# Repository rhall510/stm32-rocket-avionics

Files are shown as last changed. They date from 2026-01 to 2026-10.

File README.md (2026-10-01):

# STM32-based rocket avionics unit and active tracking ground station

 

> **⚠️ NOTE: This project is currently in active development.**
> See the [project plan](docs/PROJECT_PLAN.md) for a detailed roadmap and the [development log](docs/DEVELOPMENT_LOG.md) for regular progress updates.

---

## Overview
This project aims to build a robust avionics unit for high power model rocketry. This system will also include a ground station that mechanically rotates a high gain antenna to actively track the rocket in real time during flight and receive critical telemetry data.

The system relies on sensor fusion for onboard state estimation and uses a hybrid RF tracking method combining position/movement telemetry received from the rocket and ranging with several ground nodes to accurately place the rocket.

## Key features
* **Dual-band telemetry:**
    * **2.4GHz (SX1280):** High bandwidth telemetry and ranging.
    * **868MHz (SX1262):** Command link.
* **Active ground tracking:** Motorized base with PID control tracks the rocket's position automatically using two independent data sources (on board avionics and ground ranging).
* **Live updating GUI:** See all relevant statistics and flight path updates in real time.
* **Advanced firmware:** Built on STM32 using FreeRTOS for concurrent sensor data acquisition, data logging, RF transmission, and parachute deployment.
* **Safety first:** Robust pre-flight check routine, redundant parachute deployment logic, and failsafe state management.

## System architecture
The project is divided into three main subsystems:

1.  **Avionics (Rocket):** Onboard PCB with flight sensors, NOR flash logging, and RF transceivers controlled by a STM32G474 microcontroller.
2.  **Ground station:** Network consisting of ranging nodes and a central controlling node with a motorised tracking base utilizing position telemetry to maintain a high gain link with the rocket.
3.  **Control center:** PC based GUI for live data visualization and controlling the ground station and avionics unit.

```mermaid
---
config:
  theme: neo-dark
  layout: dagre
---
flowchart TB
 subgraph Rocket["Avionics Unit"]
        MCU_R["MCU<br>STM32G474"]
        Sensors["Sensors<br>IMU, GPS, Baro"]
        NOR["NOR flash"]
        RKT_24["SX1280 2.4GHz"]
        RKT_868["SX1262 868MHz"]
        Parachute["Parachute<br>deployment"]
  end
 subgraph Air["Ground station (controller)"]
        GS_24["SX1280 2.4GHz"]
        GS_PDOA@{ label: "<span style=\"padding-left:\">SX1262 868MHz</span>" }
        MCU_G@{ label: "MCU<span style=\"padding-left:\"><br>STM32G474</span>" }
        Motors["Stepper/Servo<br>tracker base"]
        GUI["Qt GUI<br>Data display and<br> mission control"]
  end
 subgraph s1["Ground station (ranging nodes x2)"]
        n1["SX1280 2.4GHz<br>Ranging"]
        n2@{ label: "<span style=\"padding-left:\">SX1262 868MHz</span>" }
        n3@{ label: "MCU<span style=\"padding-left:\"><br>STM32G474</span>" }
  end
    Sensors -- SPI/I2C --> MCU_R
    MCU_R -- SPI --> RKT_868 & NOR
    MCU_R <-- SPI --> RKT_24
    MCU_R -- GPIO --> Parachute
    RKT_24 -. Telemetry .-> GS_24
    RKT_868 <-. Cmd .-> GS_PDOA
    GS_24 <-- SPI --> MCU_G
    GS_PDOA <-- SPI --> MCU_G
    MCU_G -- GPIO/PWM --> Motors
    MCU_G <-. USB .-> GUI
    GS_24 <-. Ranging .-> RKT_24
    n1 <-- SPI --> n3
    n2 <-- SPI --> n3
    n2 <-. Cmd .-> GS_PDOA

    GS_PDOA@{ shape: rect}
    MCU_G@{ shape: rect}
    n1@{ shape: rect}
    n2@{ shape: rect}
    n3@{ shape: rect}
```

## Repository structure
* `docs/`: Progress logs, planning documents, and testing data.
* `firmware/`: Source code for the avionics and ground station MCUs as well as other prototyping code.
* `hardware/`: KiCad schematics and PCB layouts.
* `mechanical/`: Model files for making various non-electrical parts of the project.
* `software/`: Source code for the control center GUI application.

## Current status
Goals from the [project plan](docs/PROJECT_PLAN.md) that are currently being worked on:

##### 2\. Avionics unit
* [ ] Implement and test parachute deployment logic.
* [ ] Final field tests of full avionics unit.

*For an up to date breakdown of progress, check the [development log](docs/DEVELOPMENT_LOG.md).*

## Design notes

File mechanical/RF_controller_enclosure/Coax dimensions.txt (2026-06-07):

2.4GHz = 55mm coax length (start at 75mm - 10mm for connectors each end)
868MHz = 195mm coax length (start at 215mm - 10mm for connectors each end)

SMA connector assembly:
- Cut outer jacket 10mm from end
- Expose inner conductor 3mm
- Solder inner pin
- Add outer part and crimp on ferrule 
- Heat shrink

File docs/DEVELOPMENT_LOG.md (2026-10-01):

# **Progress log**

Regular detailed progress logs will be written here. Most recent at the top.

---
### October 1st 2026

The avionics part of the project is essentially complete (except for one remaining bug which I'm working to fix currently)! Here is a breakdown of the progress made since the last update:

#### Data integration algorithm

I started by prototyping the data integration algorithms needed to transform the raw data from sensors into a live position estimate in python. I decided to go with a 3 Kalman filter approach which each handle different parts of the tracking. These are:
- A Multiplicative Extended Kalman Filter (MEKF) for integrating gyroscope, accelerometer, and magnetometer data into an orientation estimate.
- A 2D standard Kalman filter for integrating accelerometer and GPS data into a horizontal position and velocity estimate.
- A 1D standard Kalman filter for integrating accelerometer, barometer, and GPS data into a vertical position and velocity estimate.

I used raw data recorded in multiple test runs of moving the avionics unit around in different ways to test the accuracy of these filters and tune parameters to get the best results. In the end I managed to get a fairly accurate result for the total position and orientation estimate which, while not perfect, did track my movements in the tests quite well.

#### Data integration results from a walk test

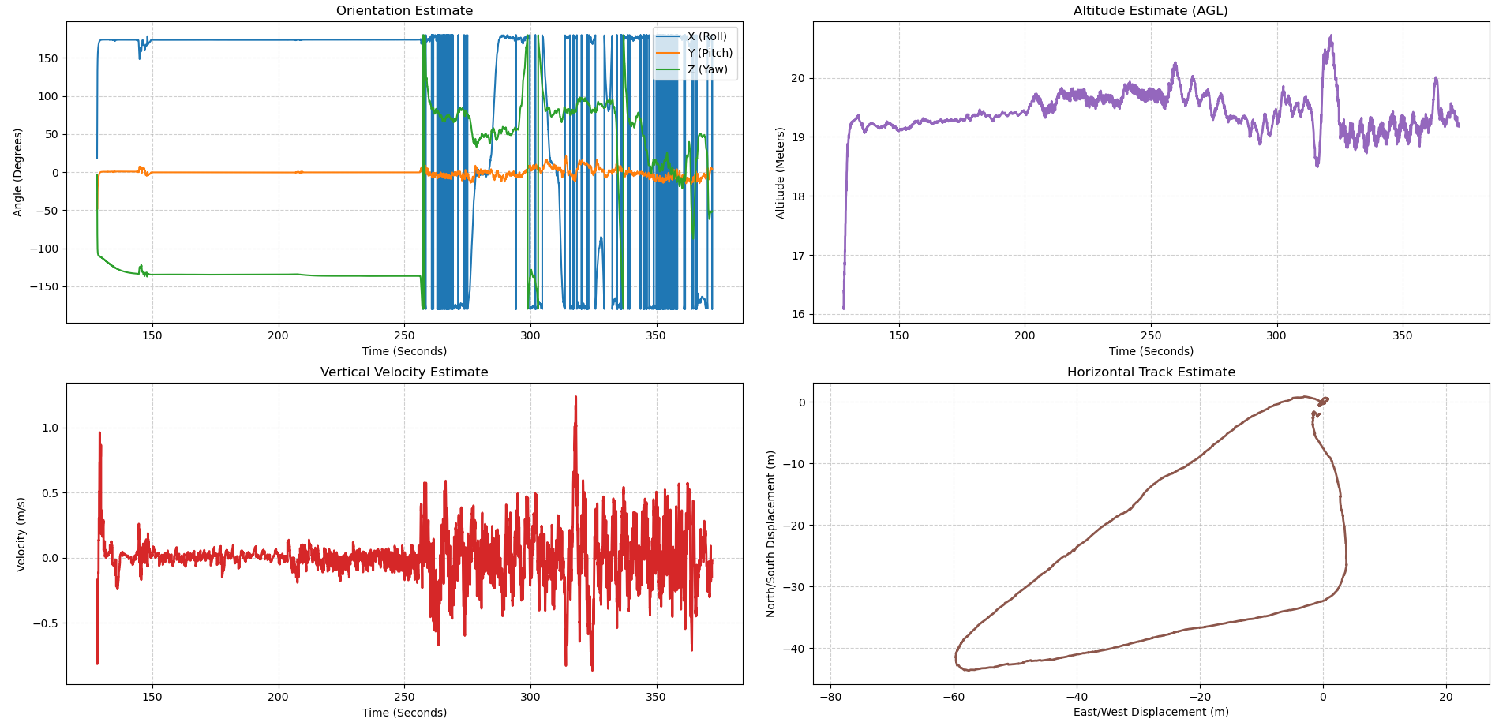
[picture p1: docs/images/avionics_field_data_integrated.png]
Data integration plots


The plots above show the results of applying these filters to the raw data aquired from a test where I walked around a track approximately 200m in length holding the avionics unit and occasionally performing other movements like rotating the unit or moving it up and down rapidly.

The vertical filter is the most accurate as the frequent low noise pressure readings can easily keep the position estimate in check to prevent accelerometer drift while the GPS prevents long term drift as ambient pressure changes slowly. This tracks the actual altitude very precisely and can capture small movements of less than a meter well.

The orientation filter is also good though it does suffer from some drift over longer periods of constant movement as during these periods the accelerometer cannot be used as a second reference vector to dampen gyroscope drift. Over the timescales expected for a model rocket flight (1-2 mins) this drift will likely not be enough to cause major issues, especially as the rocket is expected to rotate during flight which will help distribute the magnetic vectors drift correction across all axes of rotation.

The horizontal filter is the least accurate part of the system and does pose some potential problems for an actual rocket flight. The main reason for this is due to the unforgiving nature of relying mostly on the accelerometer for dead reckoning between GPS updates. There is rapid accumulation of accelerometer drift due to noise and errors in the orientation estimate leaking acceleration into the hoirizontal axes which causes a spiky looking trajectory on the horizontal plane. The drift gets substantially worse when there is rapid rotation of the avionics unit which is likely due to the fact that the rotation of the unit imparts some centrifugal force on the accelerometers which are not centered. When GPS is active however it is able to contain this drift very well and it is still able to maintain an accurate estimate of horizontal position, with possible drift of a few meters from the actual position. In an actual rocket flight which covers much larger distances than these shorter walk tests errors of this scale will be hardly noticeable.

However, GPS lock is likely to be lost during the boost phase of flight due to the high acceleration which then poses a risk of severe drift between the time GPS lock is lost and regained. Currently I plan to combat this using the network of ranging nodes planned for later in the project. These ranging nodes act as a second measurement of both vertical and horizontal position and therefore can be integrated into the Kalman filters. Ranging position estimates will be more accurate the closer the rocket is to the ground and should still work perfectly during the boost phase. Therefore, I can use the position estimate provided by the ranging nodes to correct position while the rocket is low to the ground and GPS lock is lost, then later in flight when the rocket is higher up and GPS lock is regained it can start using GPS again. In this way the two measurements cover each others weaknesses and allows a position measurement to be obtained throughout the flight to prevent drift.

#### Live telemetry on the avionics unit

So with the data integration algorithm fully prototyped I then translated it over to the avionics unit so it could run in real time. I used the CMSIS-DSP library to handle most of the matrix operations for it's high efficiency and manually coded helper functions for quaternion operations as in the prototype. I then expanded the network functions to add commands that control the telemetry output of the avionics unit via the controller node. First the home position command must be sent which instructs the avionics unit to collect samples from the barometer and GPS to set the position it is at currently as the reference position to measure displacement from. This must be done first and the unit will refuse to start telemetry without first setting the home position as a safety check. Once this is done another command can be sent to start telemetry collection which will instruct the avionics unit to wipe previously stored flight data and start up all sensors. It will then integrate all received data and periodically send back it's current estimate of position, velocity, orientation, temperature, and pressure to the controller node. The controller can then relay this data to the host PC which runs a script to display the data live.

#### Live telemetry test showing good tracking interrupted periodically by large erroneous spikes

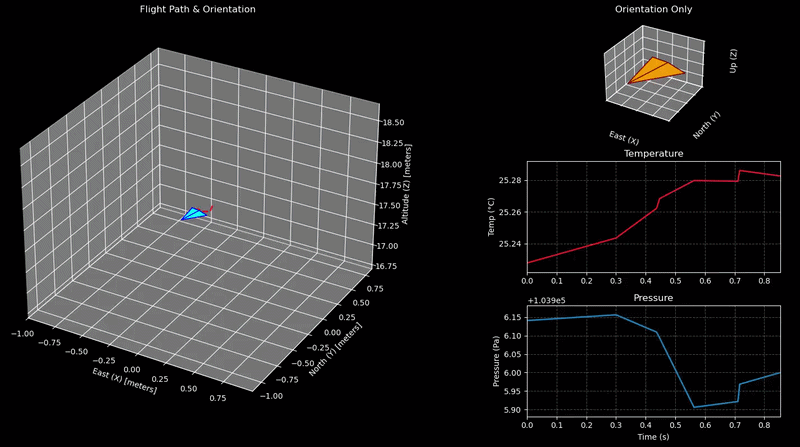
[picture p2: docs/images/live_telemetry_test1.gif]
Live telemetry test


The GIF above shows the actual live data received from the avionics unit during a test where I walked it along the same track as the previous test. The telemetry shows it follows the track very well overall but there are clear spikes in the data which appear to happen at random. Looking at the raw data reveals that these erroneous values appear in all the data types (position, velocity, orientation, temp/press) and they appear more often when the avionics unit was further from the controlling node. In addition, the raw data downloaded from the test does not show these spikes and the estimates for all data cleanly return to the real values immediately after each spike. Therefore, it is very likely these errors are being introduced in the transmission of the data from the avionics unit to the controlling node, rather than an issue with the data or integration algorithm itself. Currently I think this is likely due to the fact that the controlling node relays all packets without checking for CRC errors beforehand. I plan to add this check and run another test to see if this fixes the error ASAP.

Other than that issue however, the live telemetry link works perfectly!

#### Flight state machine

To support the parachute deployment logic a state machine was implemented to track the current stage of flight the eventual model rocket is in. It consists of 5 states with the following transition rules:

- PAD STATE: Transition to boost state when velocity and altitude are above thresholds
- BOOST STATE: Transition to coast state when acceleration (ignoring gravity) drops below threshold
- COAST STATE: Transition to descent state when vertical velocity goes negative
- DESCENT STATE: Transition to landed state when altitude and velocity are below thresholds
- LANDED STATE: No transition

The transition from coast to descent state triggers the parachute deployment logic.

I have not currently tested this state machine but I plan to as soon as possible. I would like to get a drone and attach the avionics unit to it to be able to collect data on larger and faster movements more similar to what might be expected for a model rocket launch.

---
### July 17th 2026

The data calibration stage has been completed successfully! I have written 3 python scripts which take in the raw binary data downloaded from the avionics unit and use it to calibrate the magnetometer, both accelerometers, and the gyroscope.

The gyroscope is the easiest to calibrate. Although scale factor and cross axis alignment issues can exist for gyroscopes, they are generally quite well calibrated from the factory, and it isn't really practical for me to make the precise setup required to calibrate these things without launching an entirely new project. Therefore, I decided to only focus on the other easy thing to calibrate which is the zero-rate offset. For this I recorded some data for around a minute while the unit was sitting perfectly still. The first and last 2 seconds of the data is filtered out to remove spikes caused by the pressing of the start/stop button from affecting the calibration. Then the average value for each axis was simply averaged and negated to get the offset that needs to be added to each reading. Below is the results of calibrating the gyroscope data:

#### Gyroscope calibration

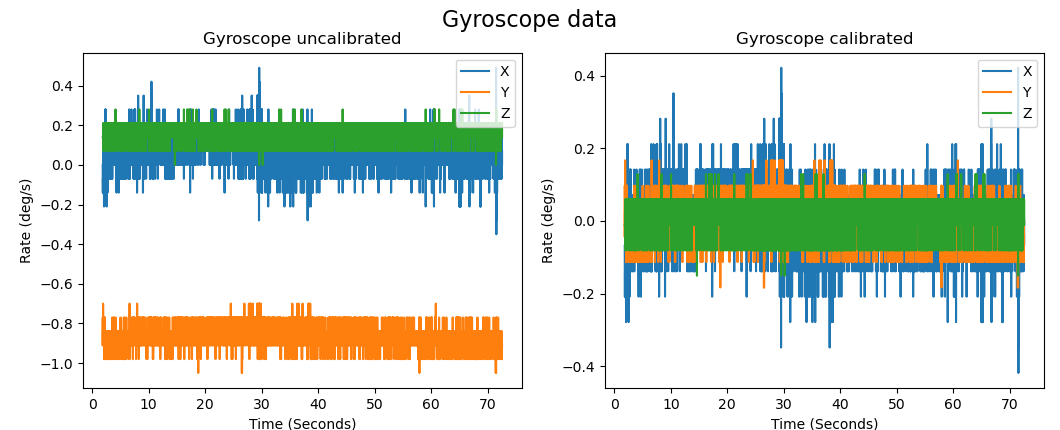
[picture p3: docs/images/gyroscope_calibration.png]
Gyroscope calibration


Next is the magnetometer. For this I used an ellipsoid fitting algorithm to correct both hard and soft iron interference. This algorithm uses least squares to fit an ellipsoid to the uncalibrated data, and then find the transforms needed to turn the ellipsoid back into a unit sphere centered at the origin. Data was collected by taking measurements continuously while I spun the unit around in my hands at all angles. Below is the results of calibrating the magnetometer data:

#### Magnetometer calibration (red wireframe is the ideal unit sphere with a red cross at it's center)

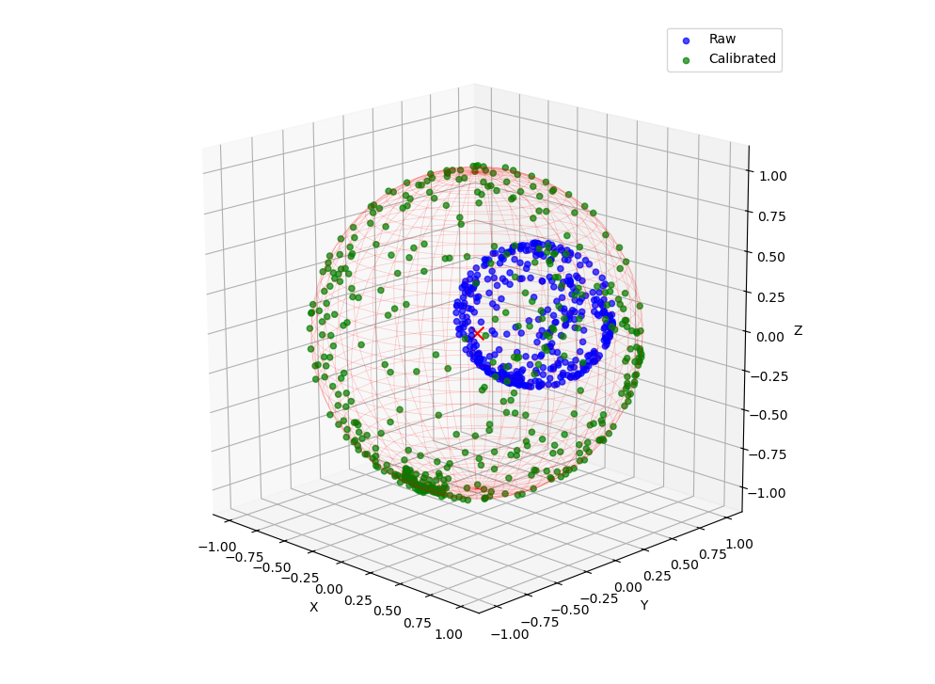
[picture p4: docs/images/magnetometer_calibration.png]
Magnetometer calibration


Finally, the accelerometers. For this I use the same ellipsoid fitting algorithm as used for the magnetometer, but with some differences in data collection and processing before calibration. While the magnetometer measures Earths magnetic field and is not affected by the movement of my hand when rotating it, the accelerometers measure gravity PLUS any additional movement when rotating it around. This will obviously throw off the calibration as it expects the magnitude of the measured force to be exactly 1, so I adapted my strategy to get more stable readings. Instead of rotating the unit in my hands, I 3d printed a roll cage which holds the avionics unit in it's enclosure rigidly in the center. This can then be placed in a bowl and rotated to any angle, and there is enough friction to hold it perfectly still.

#### Accelerometer calibration roll cage in a plastic bowl with the avionics unit held in the center

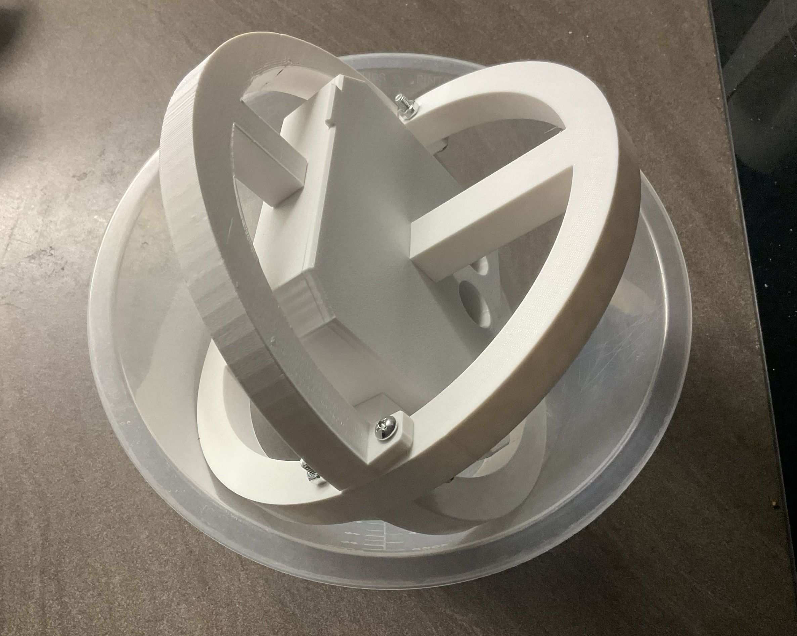
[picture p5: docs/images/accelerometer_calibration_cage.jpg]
Accelerometer calibration roll cage


Data was recorded continuously as I rotated the unit to various angles in the bowl, stopping for a few seconds at each angle to allow all vibrations to settle and get a stable reading. Of course, the raw data now contains both the stable periods and the movement when I'm rotating it in the bowl, so before calibration I added logic to first filter out all the unstable periods. To do this I calculated the variance with a rolling window of 50 measurements (half a second), and selected only data where the variance is below a threshold. I also added an additional filter to remove data recorded within 100ms of the threshold being crossed (either at the beginning or end of a settled period) as an additional buffer against including bad data. This gave nice clean measurements at various angles from only periods where the unit was completely settled.

The high-G accelerometer presented an additional problem because it has a very high baseline of noise in this low acceleration environment, meaning settled periods could not be picked out due to the noise completely swamping out the additional variance caused by movements. Therefore, I utilised the timestamps of the settled periods determined from the low-G data to filter the high-G data to only include measurements done within these same periods. This was not enough however, as the extremely high baseline noise meant an ellipsoid could not be fit well to the data, even after filtering. Therefore, an additional averaging step was introduced. For each settled period, all measurements were averaged to produce a single more stable measurement. This was done for both the high and low G data for consistency. Using this averaging method, I was able to get a good ellipsoid fit from 38 data points (one for each settled orientation) and nicely correct the high-G accelerometer data despite the extreme noise level. Below is the results of calibrating the accelerometer data:

#### Accelerometer calibration (red wireframe is the ideal unit sphere with a red cross at it's center)

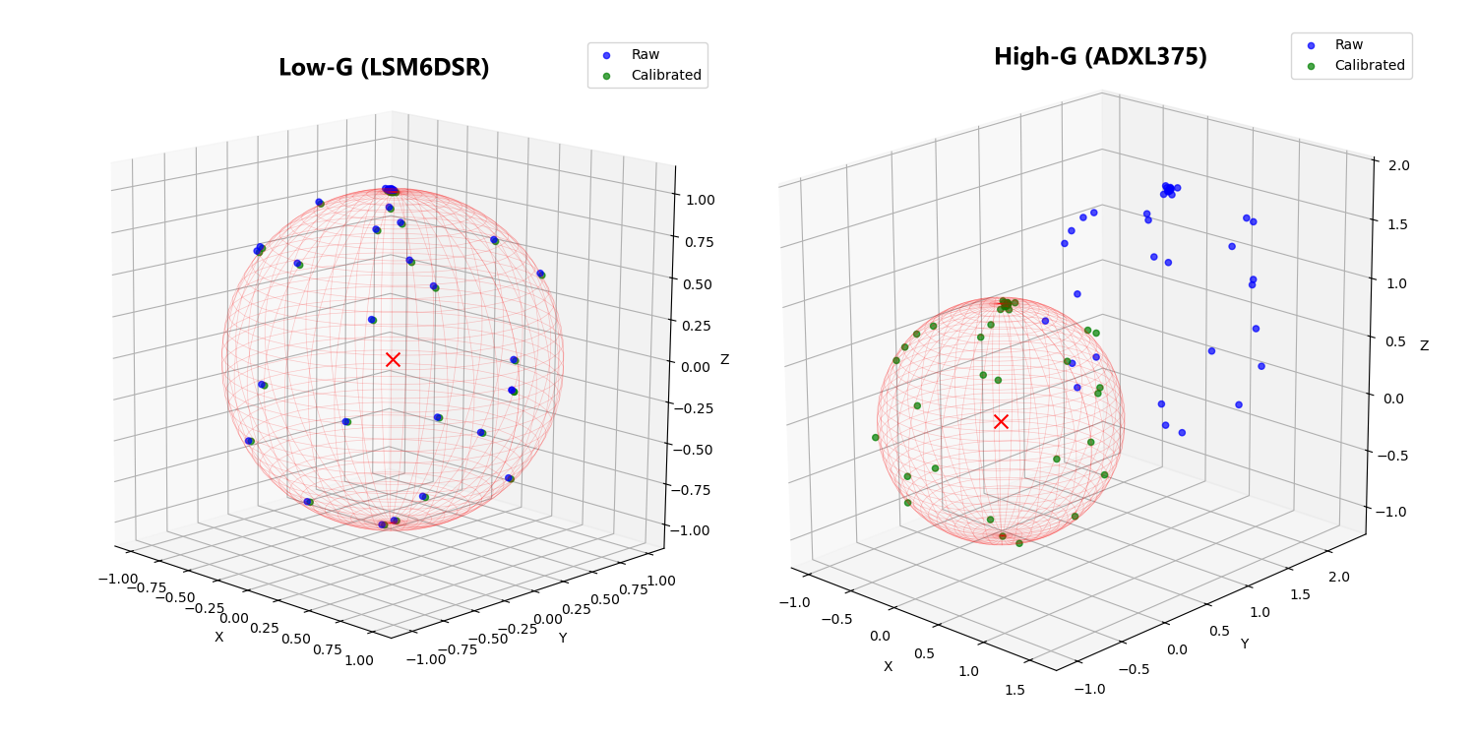
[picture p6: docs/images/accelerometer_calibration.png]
Accelerometer calibration


---
### July 16th 2026

Over the past ~2 weeks I have been working on the goals I set in the last update, and I'm happy to say all of them have now been completed!

#### Improved antenna design

After a few attempts I managed to successfully make and tune a pair of 868MHz sleeve dipole antennas. I made them by stripping a piece of RG316 coax cable to remove all but the inner conductor for around 80mm to make the top half of the dipole. Then I used a piece of 6mm diameter 0.5mm thickness copper tubing cut to around the same length for the second half of the dipole, soldered to the outer braid at the base of the exposed inner conductor portion. To keep the coax centered in the tubing I applied a few layers of heat shrink at 2 points along the length of the coax to be covered by the tubing, ensuring they were as thin as possible to not affect the velocity factor of the gap too much (this was learned the hard way with one failed attempt that used far too much heat shrink!). I also covered the exposed inner conductor in heat shrink for added stability and protection. I left a bit of length under the tubing to clip on a ferrite bead and then soldered an SMA male connector before tuning using a nanoVNA. After tuning, the inner conductor has a final length of 82mm and the tubing has a final length of 73mm.

I then 3d printed some enclosures to protect and stabilise the antennas further. These enclosures do slightly detune the antennas, making their resonant frequency decrease slightly, but the SWR at 868MHz is still <2.0 so I plan to leave them as they are currently until I know the exact final design of their environment so I can perfectly tune them at that point.

#### Sleeve dipole design (top: uncovered, bottom: in enclosure)

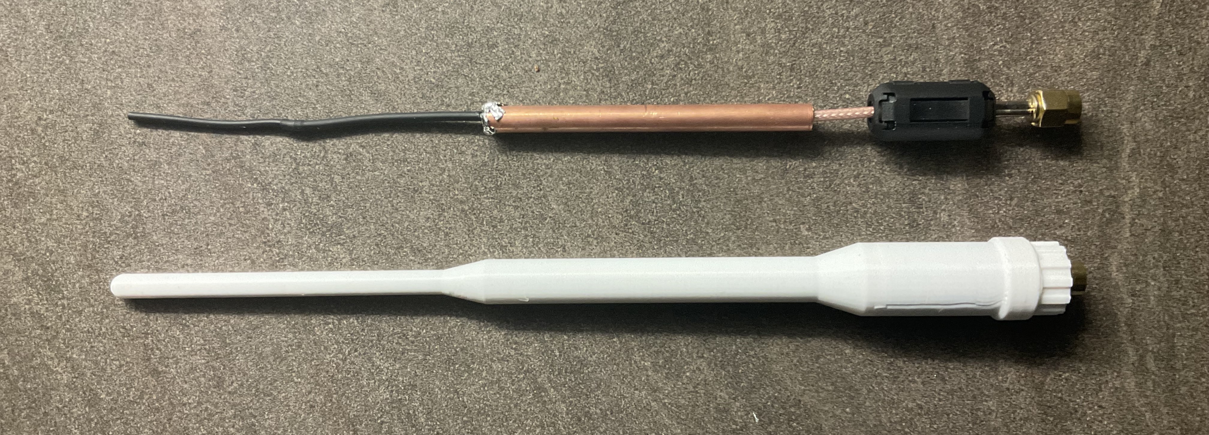
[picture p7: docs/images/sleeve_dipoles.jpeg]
Sleeve dipoles


#### Sleeve dipole final tuned nanoVNA reading (no enclosure)

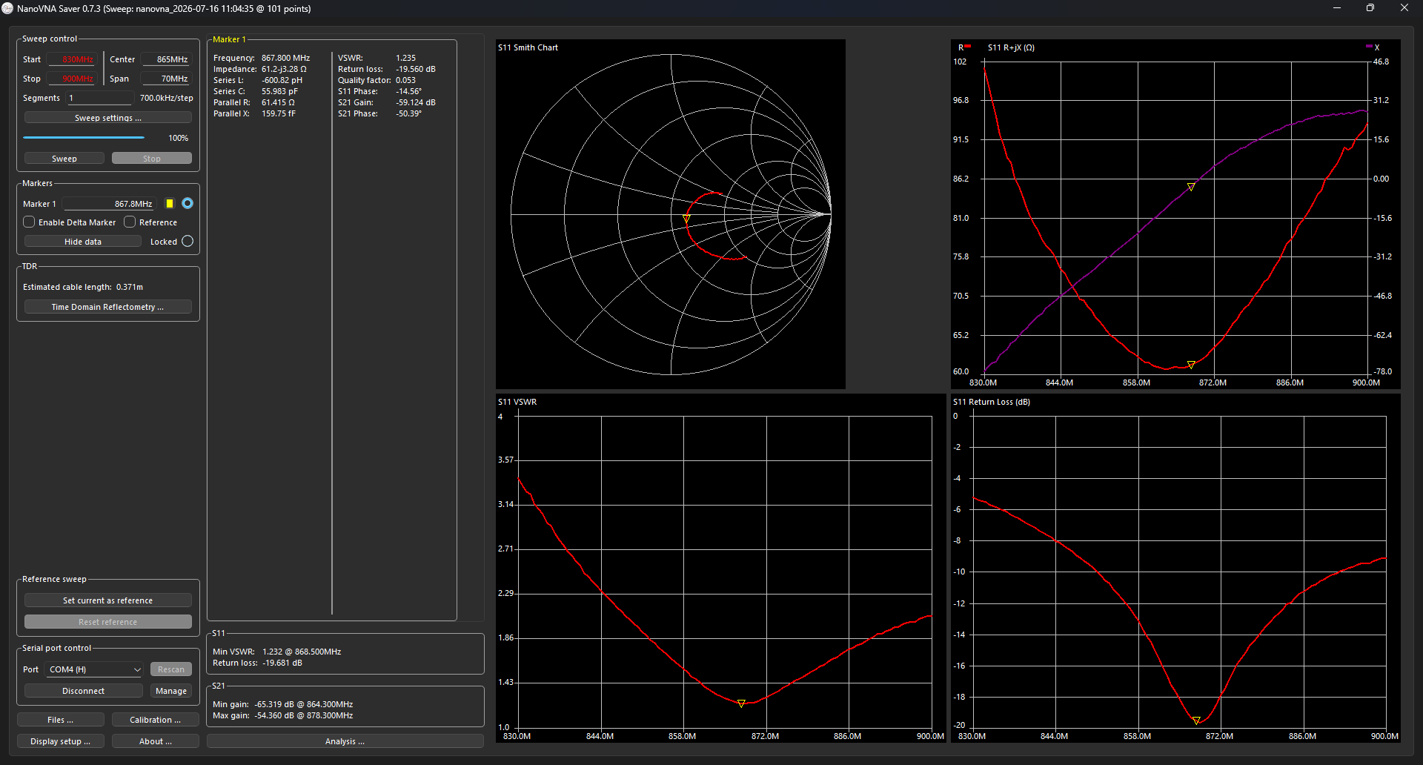
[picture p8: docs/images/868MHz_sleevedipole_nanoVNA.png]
Sleeve dipole nanoVNA


I have only made the 868MHz versions of these for now as my nanoVNA is the H4 variant which can only measure up to 1.5GHz. I have ordered a liteVNA which I will use to make the 2.4GHz variants once they arrive. It will also be more accurate for the 868MHz version too as it doesn't use harmonics to measure above 300MHz.

#### Data download routine

After making the sleeve dipoles I worked on making a robust data download routine to get stored data off the avionics unit and onto the host PC connected to the controller. The way this works is as follows:
- The controller first requests information on how many bytes of data are stored on the avionics unit over 868MHz and relays the information to the host PC.
- Once received, the controller can send a request over 868MHz to download a specific chunk of data by sending the number of bytes to download and the number of bytes offset to start reading from (or just 0s for all available data). The avionics unit will then continuously read chunks of data in the requested block and send them over 2.4GHz to the controller. The controller relays the received data to the host PC over USB.
- The host PC tracks missing blocks of packets based on the sequence number in the first 4 bytes of each packet, and if there are no additional packets received after 500ms it is assumed the transaction has ended.
- Based on the sequence numbers received, the length of data in the first received packet, and the number of requested bytes, the host PC determines which contiguous chunks of data are missing and sends another download command for each chunk, setting the number of bytes and offset values to get the correct chunk.
- This repeats until all data has been received correctly, as which point the data from all packets are concatenated into a binary file and written to disk.

This download routine seems to work well except in rare circumstances where some chunks of data seem to never be received correctly, no matter how many times they are requested. This is usually fixed by simply rerunning the routine, and it happens rare enough that I have decided not to spend too much time on it currently and work on more important stuff. Over time I'm sure I can make this routine more reliable, but for now it works well enough that I am not going to worry about it.

#### Sensor reading and data logging

I have reintegrated all the sensors into the avionics firmware in a FreeRTOS friendly way. All sensors except the GPS use interrupts to release tasks to read their data. tue to the lack of an interrupt signal the GPS must be polled which is done using a timer to trigger the polling task at 4Hz (twice the expected data rate). Additionally, previously the initialisation functions of each sensor immediately started measurements with no way to stop it. Now I have updated all the sensor drivers so they start in a 'dormant' state, primed to start measurements but not actually taking them yet. Then when ready, the main firmware can call wake up functions to start/stop measurement output for each sensor. This prevents a bunch of stale measurements building up and blocking interrupts when not needed.

To log data, each sensor reading converts the gathered data into a standardised struct containing a union of all datatypes and an identifier enum for each type of sensor data, which is then pushed onto a queue. The data logging task constantly pulls from this queue and serialises the data into a byte array which can be appended to the local write buffer. Every 100ms, driven by a timer, a task notification is released allowing the task to write the contents of the buffer to the NOR flash chip at the end of the data section. The end pointer for the write buffer is then reset and the task continues accumulating data for the next write interval. Since this is a large write operation I want to eventually use DMA for the SPI transaction but for now it is blocking.

#### Field test of data collection

With that all set up I attempted the first real field tests to ensure all sensors work correctly and gather data for analysis. To do this I 3D printed some new enclosures for the PCBs and took the avionics unit to an open field to ensure the GPS antenna had clear line of sight and there are no surrounding structures to interfere with the magnetometer. In the first test run all sensors appeared to work except the GPS, which output no measurements. This was caused by the original method of stopping/starting measurements which was to use software backup mode. This mode wipes the stored configuration in RAM which cleared the initialisation config once it was woken again. I implemented a better method which is to enable/disable the output of RMC and GGA NMEA sentences over I2C. This has the effect of stopping data output but keeps the device in full operation so the RAM contents is not cleared. After this change measurements were being output and the second field test at the same location showed all sensors including the GPS working. The GPS was also very accurate even when using the air +-4g dynamic platform model. Apart from a few discrepancies, all lat/long measurements were within 1-2m of my actual location at the time. The altitude measurements were more off (typically ~5m away from the actual altitude) but still fairly close. The GPS also did not lose it's lock when the PCB was fully enclosed in 3D printed PETG and the antenna was pointed at the ground or perpendicular to the sky which is promising.

#### Example field test data from one run

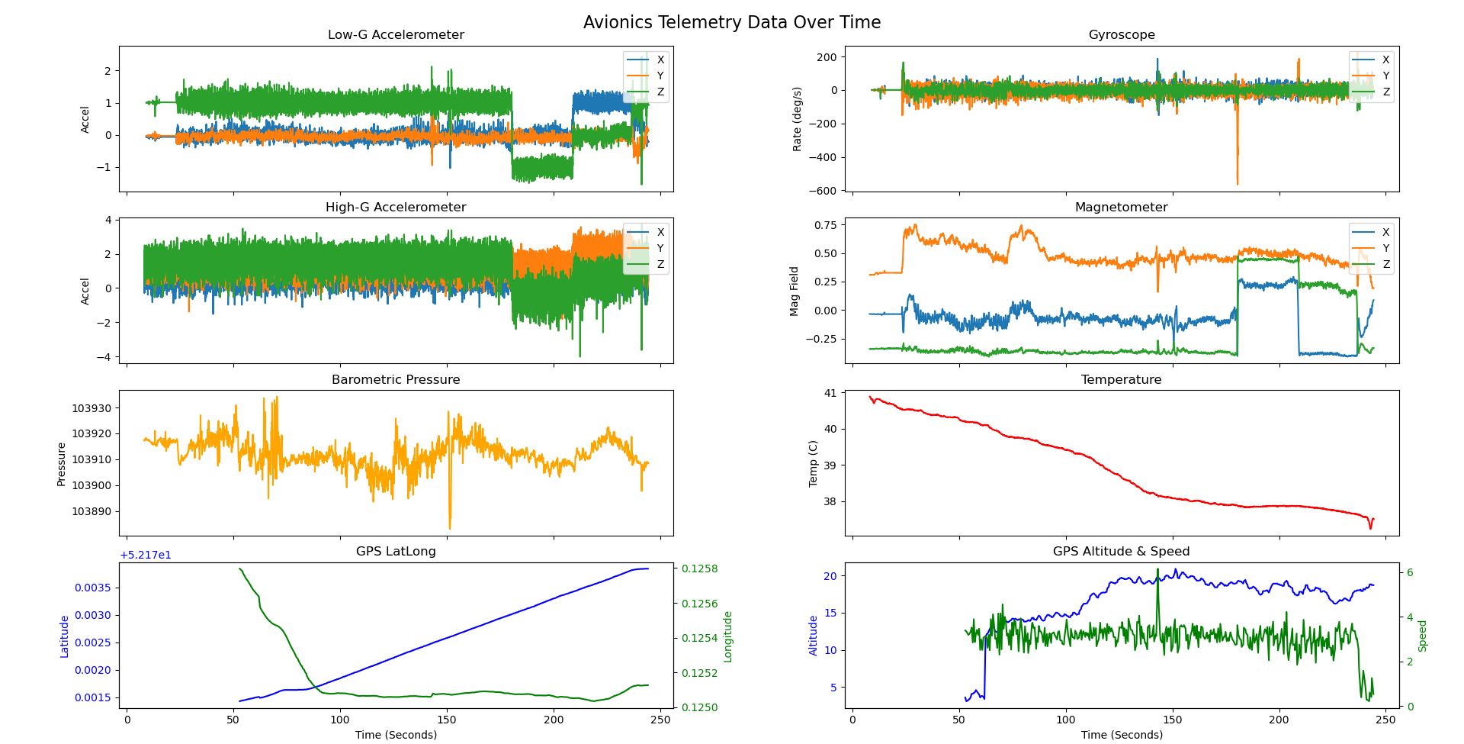
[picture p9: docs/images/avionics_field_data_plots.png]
Field test data


Overall, the sensor data seems very good! I gathered a bunch of data in the field which I now plan to use to get into the meat of the project, the sensor fusion and data integration algorithm. I have no idea how long this will take, but my goal is to first write algorithms to calibrate the accelerometers, gyroscope, and magnetometer, and then write an algorithm that can fuse all sensor data to output one robust estimate of position and movement. I will prototype this on PC first, and then attempt to translate it into efficient C code that can be run on the avionics unit once it is working well.

---
### July 1st 2026

#### Range test results

On Saturday 27th I conducted the range test on Holkham beach in Norfolk. Unfortunately it didn't go as smoothly as I had hoped because both of the radiating elements on the controlling node antennas snapped off in transit. Since we were on a beach with no equipment I couldn't repair them properly, but in an effort to make sure I got *something* I attempted to temporarily attach the snapped elements back on using some bits of metal bent out of shape to grip it. This did work and the transceivers were able to talk to each other, though I imagine it would definitely have negatively affected the results as the length of the elements was no longer precise, and the grip was quite weak so they did end up moving a lot during the test. In addition, since the antenna elements were essentially holding on by a thread, I had to settle for laying it on my bag on the ground so it was stable. If I had attempted to hold it up in the air as I had originally planned they would have almost certainly fallen off again.

So not ideal and I will definitely be repeating it taking more precautions to get it there in one piece, but for now I do have this data:

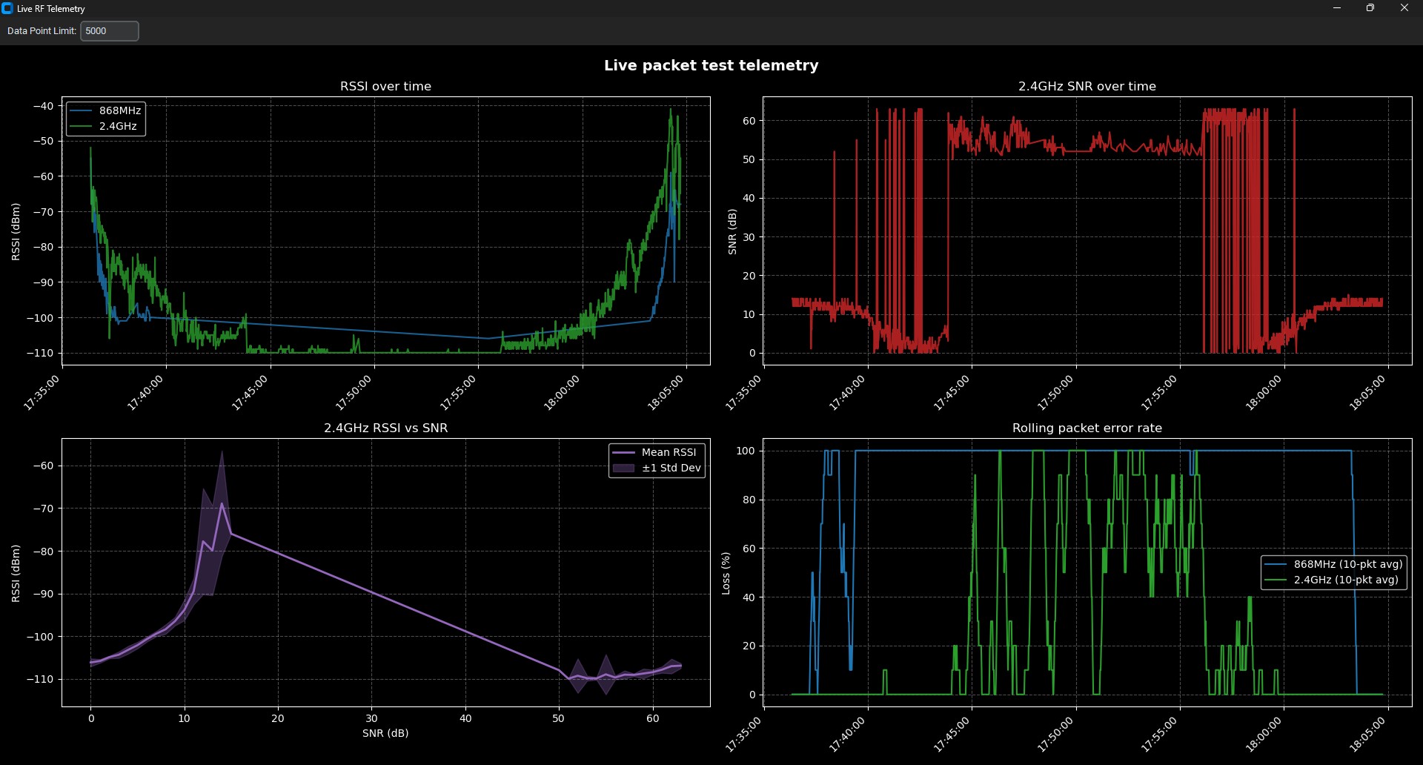
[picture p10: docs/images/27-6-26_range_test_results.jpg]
Range test results


These graphs were obtained during the test, where the controller was on the ground and the receiver was walked away around 1.5m off the ground before coming back again in the second half. There are graphs of RSSI over time for both frequencies, SNR for 2.4GHz, RSSI vs SNR for 2.4GHz, and rolling 10-packet error/missing rate for both frequencies.

The 2.4GHz signal seems to have travelled much further than 868MHz which is expected due to the fact that it uses LoRa rather than GFSK. At the stopping point (~550m away) before turning around and walking back I actually decided to risk it and hold the controller off the ground slightly (maybe only about 60-80cm) and it did regain signal again. That is the sudden jump up in 2.4GHz RSSI you can see in the second half of that graph. So maybe if I didn't have to worry about the elements falling off it could have gone further. In the end it seems like the 868MHz signal stopped entirely at only around 100m, while 2.4GHz could have potentially gone further than 550m. The lower limit of RSSI where packets were detected seems to have been -110dbm for 2.4GHz and -100dbm for 868MHz, which are both around 5dbm higher than the transceiver sensitivities would suggest. I was hoping for better results, but I think given the issues with the broken antennas I can't really complain too much.

There was also an issue with the SNR jumping up to the 50-60 range when it get's too low. This is due to mistakenly interpreting the SNR value as an unsigned integer when it should be a signed integer, meaning negative values wrapped around.

#### Next steps

This range test highlighted a few key issues that need to be addressed in the next test. It will likely be a while before I have another opportunity to do a range test so I have plenty of time to prepare.

Here are a few things I am thinking to improve reliability and get the most insight out of the next test:
- Replace the antenna design with sleeve dipoles. Currently I am using ground plane monopoles which, especially for the 868MHz ones, are quite bulky due to the five elements all sticking out at angles. This is the main reason two of them were broken in transit, and it also necessitates a bit of an awkward enclosure design to hold them out away from the PCB which makes the enclosures awkward to transport too. Switching to sleeve dipoles will enable a much cleaner, compact, and robust setup as the antennas can stand straight up attached to the PCB SMA connectors and it will be easier to detach and reattach them for transit.
- Redesign improved enclosures for the PCBs which are more portable and have attachment points on the bottom to enable them to stand on top of some sort of mast to lift them off the ground.
- During this test distance was recorded by the person walking using their phones GPS. Eventually I want to use the 2.4GHz transceivers ranging function, so to test that I could set up the test so that between each test packet the 2.4GHz transceivers range each other and record that distance. This can then be compared to the GPS distance to see how accurate it is.

Since it will be a while before the next testing opportunity I don't need to do all of this now, so I plan to redesign the antennas and enclosures and then work on other stuff until the next opportunity comes around. Here is what I plan to do over the next few weeks:

By 5th Jul: Build and test sleeve dipole antennas. Design new enclosures for the PCBs with sleeve dipole antennas.
By 17th Jul: Write and test robust data download routine. Reintegrate avionics sensor reading and storage writing tasks in FreeRTOS.
By 19th Jul: Collect field test data on avionics board. Start working on calibration and data integration algorithms.

I may be able to get all this done faster than the dates written here but I've just given myself more time in case I run into any issues which take a while to solve, which probably will happen! I plan to try making my own sleeve dipoles first but if it takes too long then I will just use commercially made ones as I don't want to be spending ages held up making antennas, which isn't really the main focus of this project.

---
### June 26th 2026

Over the past 2 weeks I have been working on getting both the RF controller and avionics boards in a state where they can be used for a more robust range test of the transceivers. There were a few challenges which took a while to figure out but they are finally ready to go now I think!

Both boards are now fully able to handle RF communication between each other. The firmware uses shared drivers for the low level functionality of each transceiver (SX1280 and SX1262) while the main file implements the specific handling of the data going to and from the transceivers. For each transceiver there is a FreeRTOS task driven by a task notification which reads any incoming packets, deconstructs them into a standardised packet struct, and places them in a queue ready to be received by the transcation manager task. Since the SPI bus is shared between the transceivers, all operations are protected by a mutex to prevent collisions on the bus.

The transaction manager task operates a state machine that calls specific handler functions based on the current state it is in. These handler functions all take in the most recently received radio packet (and USB packet for the controller) and return the state the transaction manager should switch to when it finishes (which can just be the same state). The default state is the idle state, in which the controller will continuously check the USB command queue for new commands to execute while the avionics will check the radio queue to check for new radio commands to execute. Once a command is received it will return the new active state, causing the transaction manager to execute the handler function. This architecture allows for easy maintainability and expansion later with new commands as each state has it's own separate handler function which can lead into any other if required for complex protocols.

So far I have implemented 2 basic protocols for the boards to communicate over RF:
- The first is the discovery command, which runs every X seconds (currently 4s) on the controller and is independent of any user supplied USB command. In this state the controller first broadcasts a discovery packet to the network broadcast address (0xFF) and waits 500ms for any replies. Once received by the avionics board, it will send back an ACK packet to the controllers network address to notify it is ready to go. Currently replies received by the controller are simply sent as a status packet over USB to the host PC.
- The second is the packet test command. This command is started by the user sending a packet test start command over USB and is intended for testing round trip packet reception with a specific network node. The user supplies the target network address and the controller then begins sending packet test packets to that address which contain a byte representing the channel the request was made on (0 = 868MHz, 1 = 2.4GHz) and 4 bytes for a sequence number. The receiver then echoes this packet back to the controller which listens for a 500ms window. Only one packet test command is active at a time and the channel it is requested on switches each loop to test both transceivers. Statistics such as RSSI and SNR of the received packets are collected and sent over USB to the host PC.

#### Upcoming improved rangetest

Way back at the start of the year I did a range test of the SX1262 transceivers using a very crude breadboard and arduino hardware implementation. Because it was just a bare breadboard the electronics had no protection and the antennas were literally swinging about held up by flimsy wires, which lead to unreliable and poor results.

I now plan to repeat this range test using the new and improved hardware I have made over the past 6 months. This will improve on the previous range test in the following ways:
- Custom PCBs ensure strong stable electrical connections between all components rather than using flimsy wires
- Using STM32 MCUs rather than arduinos enables much better control over the hardware using things like FreeRTOS to implement concurrent task management instead of blocking waits
- 3d printed enclosures ensure the PCBs and antennas are held rigidly in optimal positions
- Having both transceivers active means I can test them both simultaneously instead of just the SX1262
- The controller requesting each packet and receiving a response means communication is now tested both ways instead of one way
- The serial terminal, now with a live plotting function for packet test data, allows live graphical viewing of the data in the field

I hope these improvements will lead to more reliable and better results. I am hoping for a minimum of 300m of reliable reception from the SX1262s and 1km from the SX1280s to consider it a success. I am planning to go to a large open beach tomorrow where I will carry out the range test with the help of my family, and I will report back afterwards!

#### Other stuff

There is currently a persistent bug where the SX1262 sometimes fails to receive any packets properly upon initialisation, despite seemingly receiving and executing SPI commands properly. I would estimate this happens around 60% of the time, while the other 40% of the time it boots up and responds normally. I have tried to figure out the cause of this but to no avail so far. To get the range test done I have left this bug for now as I can just reset it until it boots up normally, but this will definitely need to be fixed for the future.

I have also stripped out pretty much all of the previous sensor and storage related code from the avionics firmware for now to keep it lean. I will add this all back in gradually in a way compatable with FreeRTOS later.

---
### June 12th 2026

I have started writing some basic USB functions for the RF controller which use FreeRTOS for task scheduling. It can currently read incoming messages sent from a connected host PC and echo them back out. Initially there was some strange behaviour going on where if I enabled a task that sent out test packets to the host PC periodically then it could no longer read incoming packets, even though they are entirely separate from each other. However, I eventually figured out that it was due to a stack overflow in the sending task as I set the stack size too small. It was not caught immediately because stack overflow detection was turned off in the FreeRTOS config by default, but it is now for the future.

I have also made a basic custom terminal GUI in python which can connect to a serial port and send and receive messages. It also has other QoL features like live logging to a file with prefix filtering and customisation of line endings for future flexibility. This will certainly come in handy for testing this and other devices in the future.

I now have a rough plan for how I'm going to structure the firmware for the RF controller. The USB tasks are already set up to receive commands and send back data/status messages. Commands will be added to a queue which will be processed by a central transaction manager task. Because my network architecture dictates that only one transaction can be ongoing at a time it should be simple to design a state machine that pulls from this queue, executes a transaction, and then waits for the next command. Incoming USB commands are handled by the tinyUSB Rx callback which releases a task notification, and a similar mechanism will be used for reading from the radio modules when packets arrive. For sending packets I intend to implement a function which either uses DMA or blocking transfers, using the transfer size to determine whether it would be worth the overhead to use DMA.

---
### June 10th 2026

The device descriptor bug is finally fixed! I tried all sorts to attempt to resolve it and nothing seemed to work, but in the end after determining the MCU was getting stuck in the default handler infinite loop using serial wire viewer statistics I narrowed down the issue to missing definitions of the USB_HP and USB_WakeUP IRQ handlers. Once those were implemented the USB connection worked perfectly on bare metal. I then tried to re-enable freeRTOS and it began failing with the same device descriptor error again, and SWV statistics showed it was hanging in the vPortValidateInterruptPriority(). The only interrupts I had not explicitly set the priority for were the 3 USB IRQ handlers as I thought they were handled by tinyUSB, but after manually setting their priorities to above the required level this was also fixed and I now have a stable USB connection with freeRTOS enabled.

I now need to plan how I want to design the firmware to handle simultaneous USB and RF transfers, as well as handling various networking packets which require different behaviours.

---
### June 8th 2026

I have spent the last week or so designing and printing an enclosure for the RF controller PCB and starting to write the firmware to drive it.

The enclosure is used to both protect the PCB from the elements if used outdoors (which it will eventually be) and enable stable placement of the antennas for the transceivers so they are a good distance apart and vertically oriented to enable good horizontal signal coverage. The enclosure holds the PCB to the base and antennas to the masts with clamps that are screwed in. Even though the 868MHz and 2.4GHz bands do overlap, the antennas are held ~130mm apart which should provide good separation to reduce any stray interference between the two frequencies and reduce the risk of swamping during transmission.

#### RF controller enclosure outside

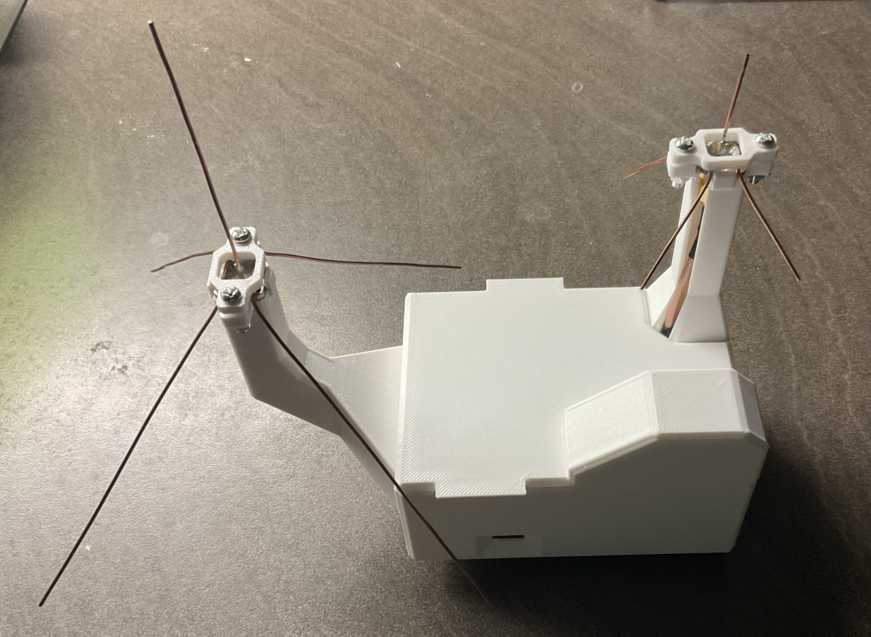
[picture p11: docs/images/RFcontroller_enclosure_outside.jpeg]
RF controller enclosure outside


#### RF controller enclosure inside

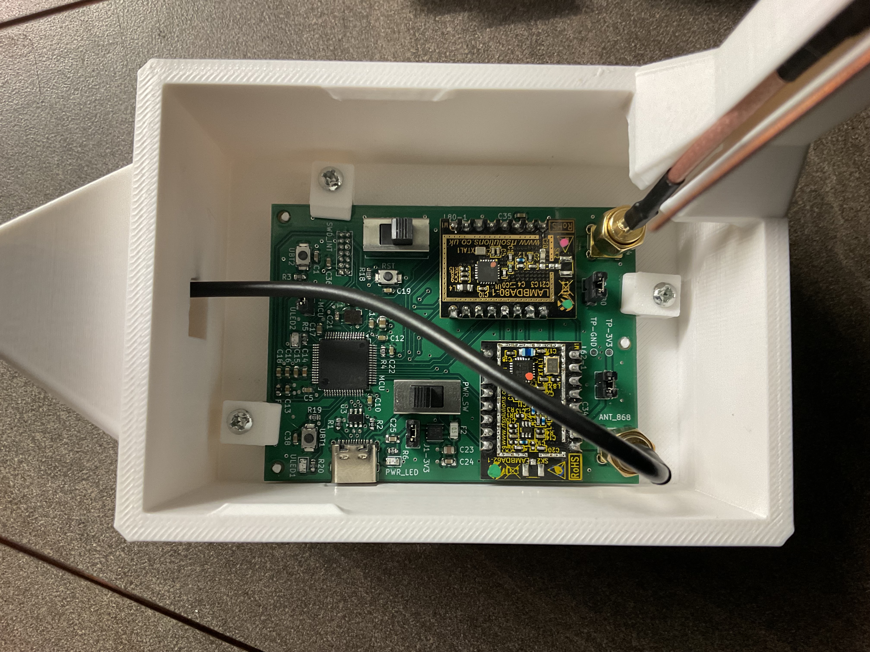
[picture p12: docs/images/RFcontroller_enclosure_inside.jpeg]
RF controller enclosure inside


Alongside this I have started writing the firmware to drive the RF controller. I made a clean project and integrated HAL, TinyUSB for driving the USB connection, and FreeRTOS for concurrent task management. I plan to use this as an opportunity to learn FreeRTOS in a smaller project before attempting to implement it on the larger avionics board. So far I have got to the point where all the basic initialisation code is there and everything is integrated and seemingly working fine. Windows does detect a USB device is connected when I plug it in but the device descriptor cannot be obtained properly. I will attempt to fix this next and get the USB connection fully working.

---
### May 31st 2026

The RF controller PCB and components finally arrived and I assembled the board using the same method as the avionics board (hotplate reflow for the SMD parts and soldering iron for the remaining through hold components). Assembly went perfectly except for some easily fixed solder bridging on the MCU pins and one of the pads of the 16MHz crystal not soldering correctly. After assembly I brought up the board in stages using the power isolation jumpers and observed no issues. A stable 3V3 was output onto the power rail, the power LED turned on, and no components significantly heated up. The MCU was detected by STLINK and was able to be programmed, and I used cubeMX to generate a simple project that sent a message continuously over USB to a virtual COM port on the connected PC. Using this I was able to detect the device when it was plugged in and read the sent messages perfectly!

The next step is to design and print an enclosure to contain the board and antennas in one easy to transport package that also protects sensitive electronics from the elements.

#### RF controller bare PCB on the hotplate

RF controller bare PCB

#### RF controller fully assembled PCB

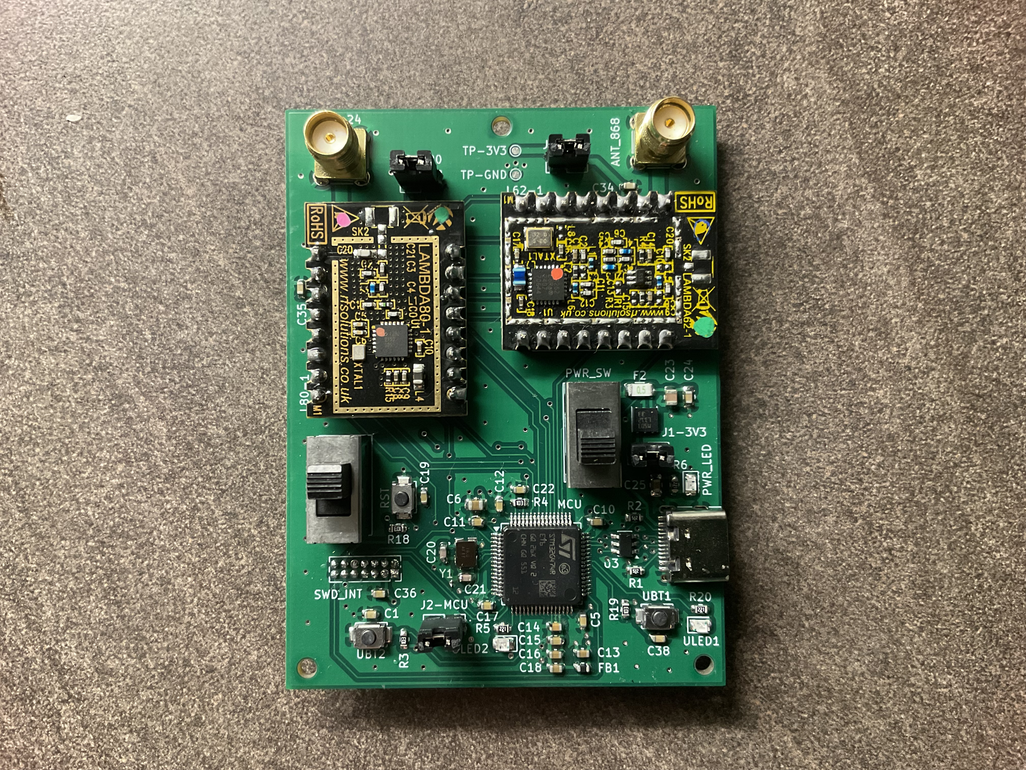
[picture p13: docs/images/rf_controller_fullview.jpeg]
RF controller assembled PCB


---
### May 14th 2026

The layout for the RF controller PCB has been finalised and ordered. Once it arrives I'll begin assembling and testing it, and then I can use it for testing the main avionics board command link. As mentioned earlier, this PCB is essentially a stripped down version of the avionics PCB with only the MCU and LoRa transceivers.

#### RF controller PCB schematics (microcontroller section)

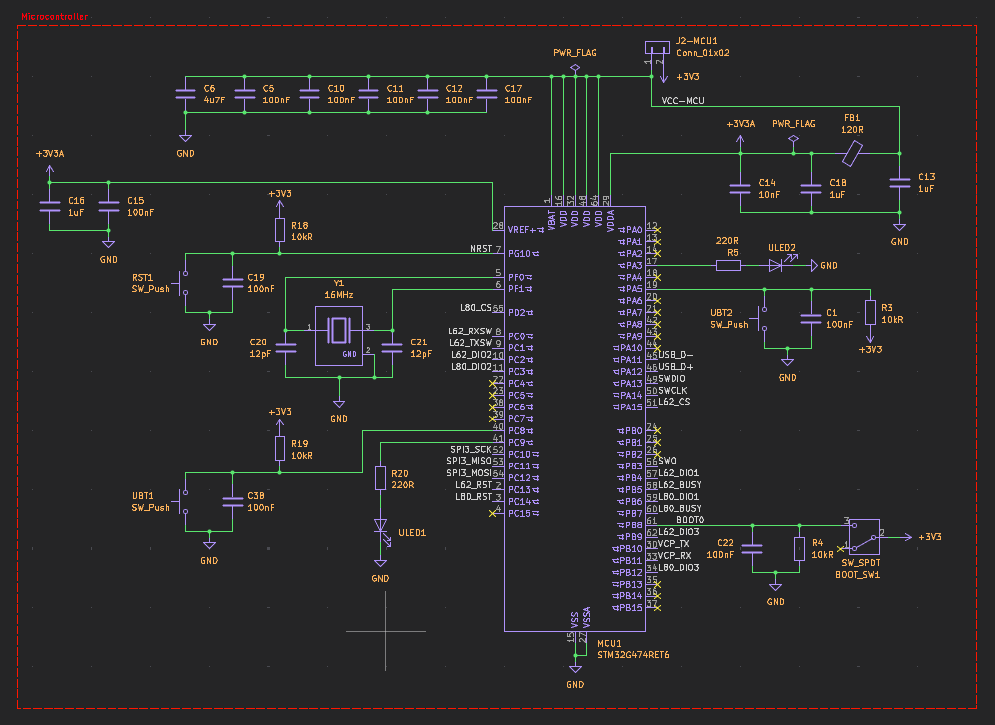
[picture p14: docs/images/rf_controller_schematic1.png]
Finalised RF controller PCB schematics part 1


#### RF controller PCB schematics (transceiver and SWD section)

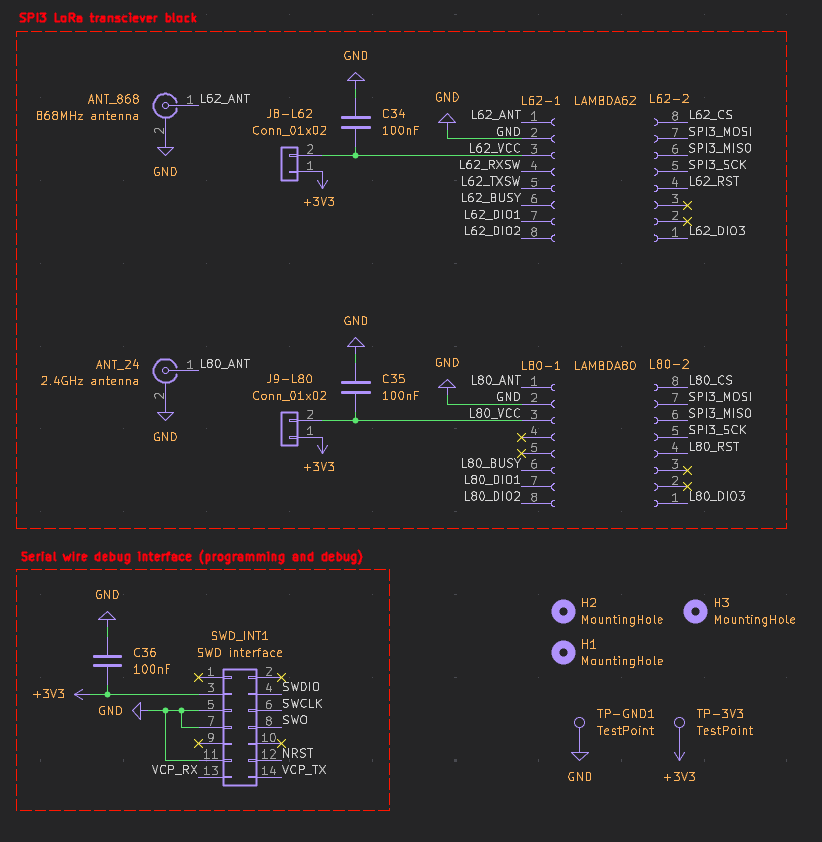
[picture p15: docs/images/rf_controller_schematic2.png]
Finalised RF controller PCB schematics part 2


#### RF controller PCB schematics (USB and power section)

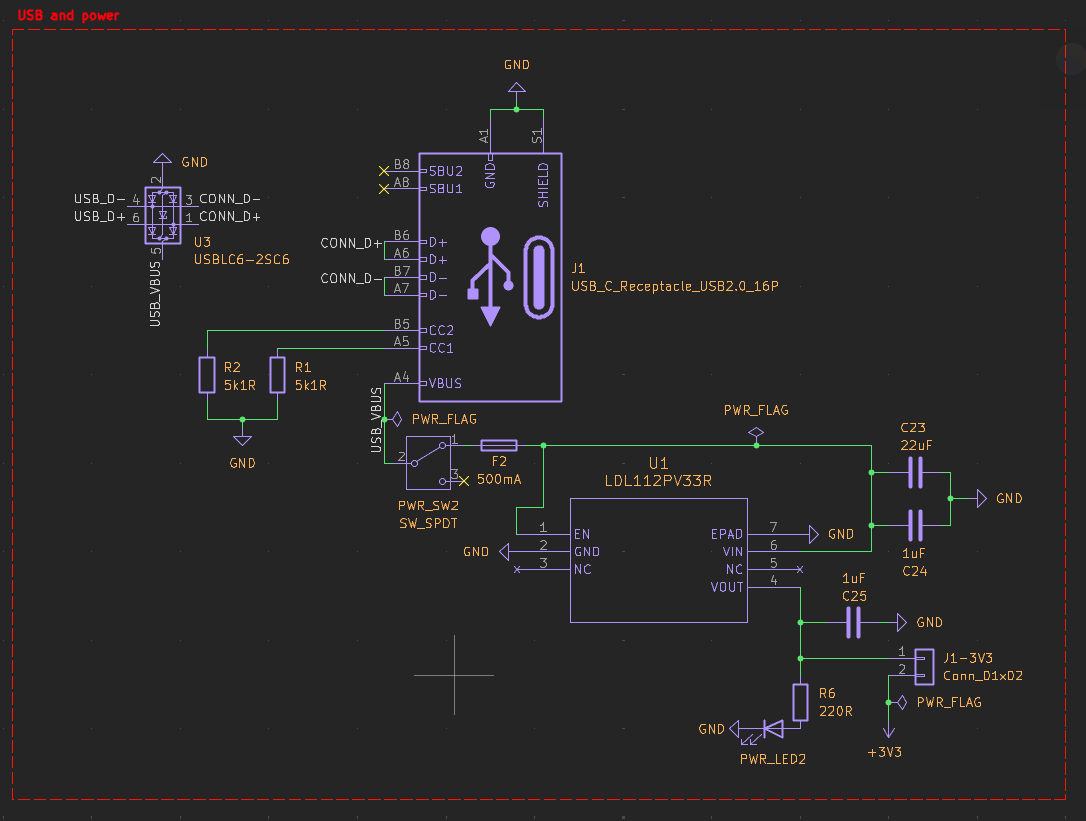
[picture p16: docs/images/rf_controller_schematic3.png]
Finalised RF controller PCB schematics part 3


#### Finalised RF controller PCB layout (top and bottom signal layers in red and blue)

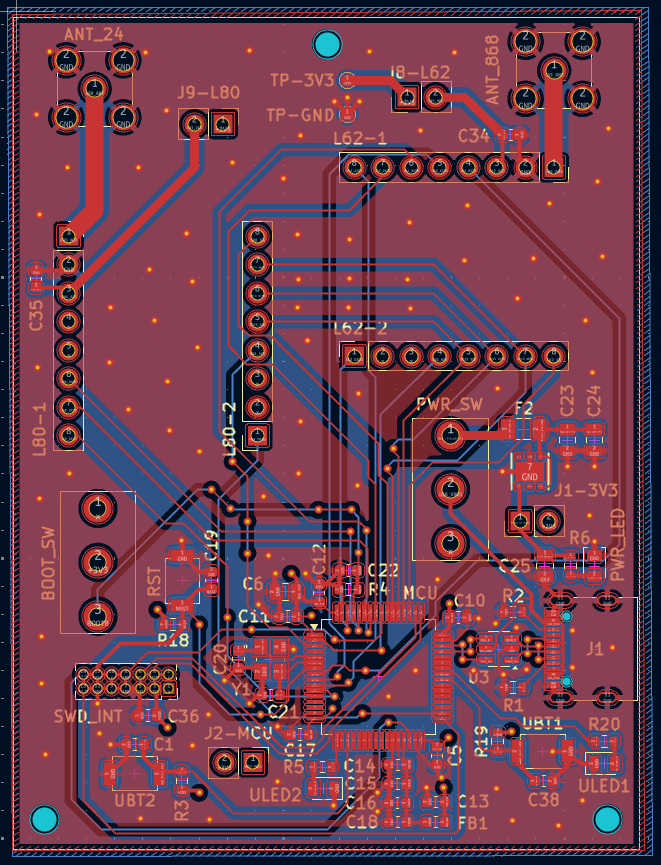
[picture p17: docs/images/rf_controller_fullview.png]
Finalised RF controller PCB design


---
### May 12th 2026

I have been thinking about how I want to handle the command link and I have written up a plan [here](dev_board_planning/Command%20link%20plan.txt). In short, I plan to use a master-slave relationship where the central controller (eventually to be connected to the ground station computer) always initiates transactions which the other nodes in the network can respond to. I have expanded the plan to take into account the possibility of multiple slave nodes rather than just the single rocket avionics unit due to the fact that I have been exploring the idea of using a network of 3 SX1280 modules to triangulate the position of the rocket. This would replace the current plan to use phase difference of arrival to track the azimuth of the rocket and allow for a more accurate external determination of the rockets position to complement the on board sensors. However, it does require more setup and a more comprehensive network architecture to handle potential collisions. I am leaning towards doing this though as it would be nicer to be able to externally track the rocket in all 3 axes.

I have started designing a smaller PCB for the controller node which just contains an STM32G474RET6 MCU and the LAMBDA80 and LAMBDA62 transceivers. It also includes a USB connection to enable communication with the host PC. This version of the controller is just for testing as it does not include all the features that the full ground station PCB will need to have to control the motors, it's just much nicer to work with a neat PCB rather than breadboards, especially for this project where it will likely be a good while yet until I progress to making the full ground station PCB. So far I have made the schematic for the board and I will do the layout and routing next. It will be very similar to the main avionics board but just omitting all the sensors, storage, and parachute deployment sections. It also includes a USB-C connector from which is draws it's power. Power is stepped down to 3V3 by an LDL112PV33R LDO regulator instead of a buck converter for simplicity and less potential EMI from a switching power supply. I designed the main avionics board with a buck converter for efficiency reasons since it is battery powered rather than USB, but I may end up eventually switching that to an LDO as well in the final design as efficiency is not the main concern for short flights.

---
### May 6th 2026

I have finished implementing a small testing script which decodes the raw data transmitted from the avionics unit. The script reads a binary file of concatenated data packets and first parses the packet headers and contents to identify any missing packets by checking the sequence number. It then concatenates all the actual data contents of the packets and splits it into chunks by the sync word. Each chunk is checked to ensure it's reported and actual length match and the CRC is correct. Finally, for each validated chunk the data within is parsed and added to arrays containing the data and timestamps for each sensor reading.

Initially using this script I saw there were no data packets from the LSM6DSR or MAX-M10S modules after decoding the received binary. Using a hex viewer I saw there were GPS data packets in the raw binary, but they were not being parsed correctly. I eventually discovered that the missing MAX-M10S packets were due to the type bits in the data header being set wrong, making the decoding script think they were part of the magnetometer readings. However, there were no LSM6DSR packets at all. I did some debugging and found that the data ready interrupt was no longer firing even though it worked previously and I had not touched the driver code apart from to log the data, which should have no effect. In the end I realised that the lack of interrupt firing was due to the LAMDBA62 modules DIO1 pin being mapped to the same pin number as the LSM6DSR INT pin, and although I did not set up an EXTI interrupt on the DIO1 pin, I had mistakenly set the GPIO mode as IT_RISING, which masks the other ports interrupts in the HAL initialisation function. Changing the mode to input solved the problem and I was able to log, transmit, and decode data from all sensors successfully.

During transmission there were a few dropped packets. There is still no mechanism for requesting resends of packets, but that is the next priority. To do this I plan to set up the command link on the 868MHz band next.

#### Plotted test data from 100s of the board sitting stationary

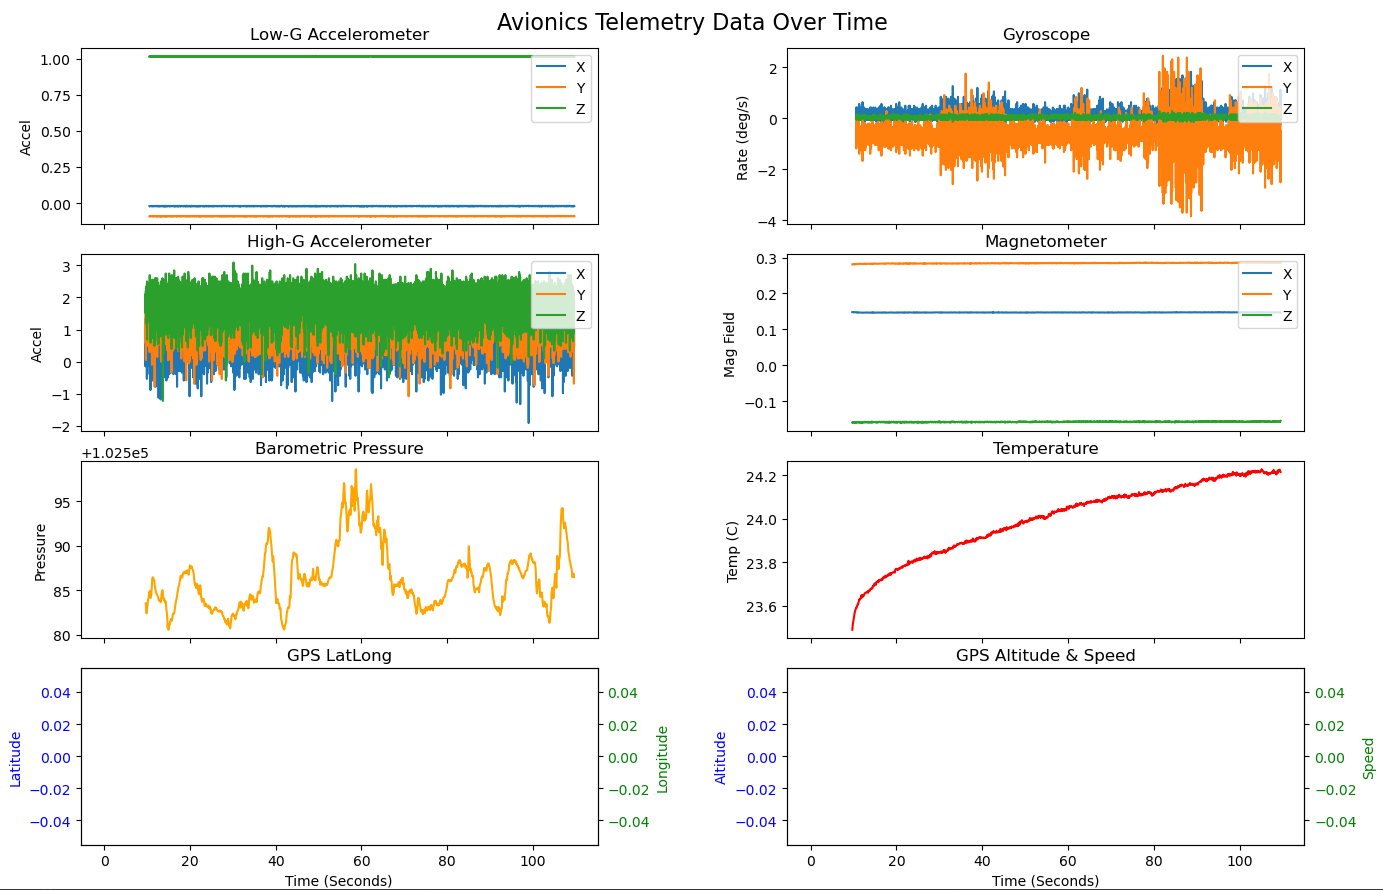
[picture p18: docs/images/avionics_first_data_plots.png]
Plotted test data from 100s of the board sitting stationary


\* Note: GPS data is currently empty as this was done indoors

---
### May 3rd 2026

Over the past two days I have finished implementing and debugging data logging and a basic download link between the main avionics board and a host PC. Data logging has been more thoroughly tested now seems to work perfectly after ironing out a few issues. See the test logs [here](dev_board_planning/Data%20logging%20tests.txt) for more details.

I also spent a lot of time testing and debugging the data transmission function. I made two 2.4GHz ground plane monopole antennas in the same design as the previous 868MHz ones and connected them to the transmitter (avionics unit) and the receiver (nucleo-g431kb board connected to the host PC). Unfortunately, as I only have the nanoVNA-H which only measures up to 1.5GHz, I cannot tune the antennas perfectly for 2.4GHz so I just cut them to as close to the theoretical perfect length as possible.

#### 2.4GHz ground plane monopole antenna

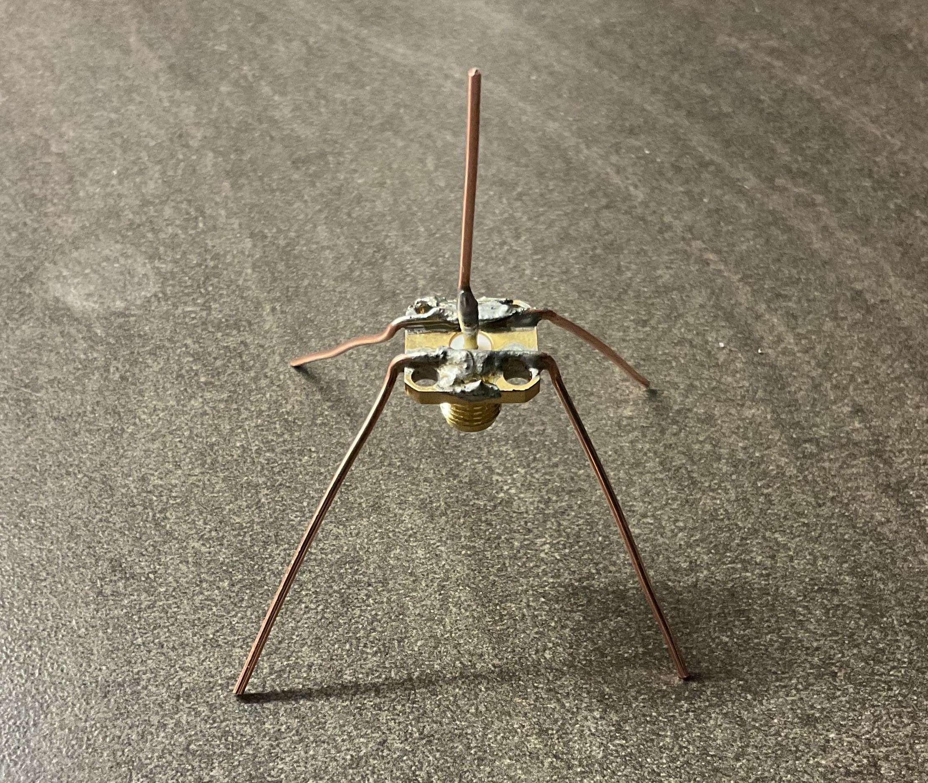
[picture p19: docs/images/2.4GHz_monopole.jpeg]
2.4GHz ground plane monopole antenna


#### View of the fully assembled avionics unit with the 2.4GHz antenna and ST-Link attached

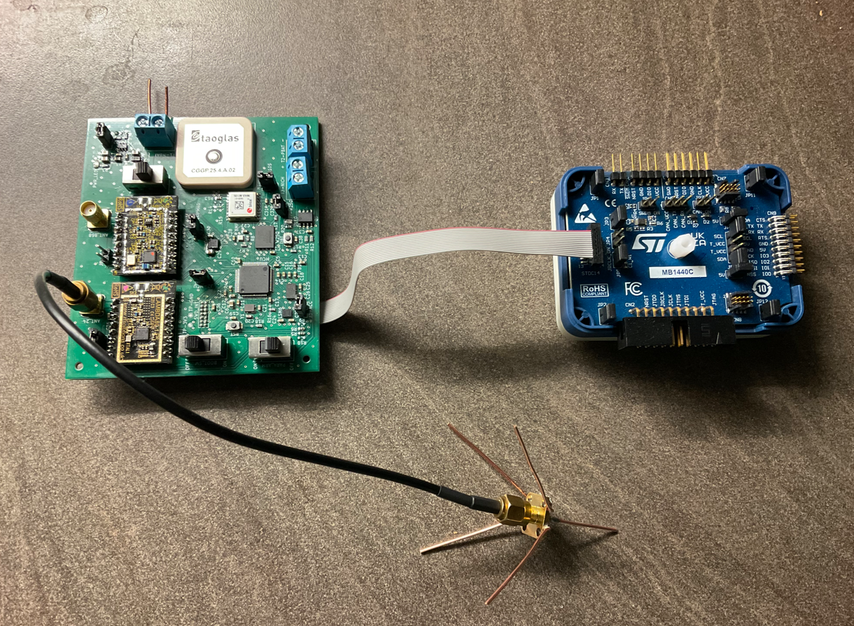
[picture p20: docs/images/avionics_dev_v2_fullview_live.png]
Avionics unit with 2.4GHz antenna


Initially the receiver was not receiving packets but it seems most of the issues were caused by some incorrect configuration options and not properly waiting for the transmitter to finish sending a packet before queueing the next one. After fixing the options, implementing proper delays, and adding a proper header and terminator to each packet we now have a working data download link which can transmit data to a host PC via a connected receiver over UART at around 200kb/s. There is currently no error correction in the download protocol though.

The next step is to properly decode and parse the raw binary data received and implement error correction in case of any missing or malformed packets.

---
### May 1st 2026

Today I finished the main functionality of both LAMBDA drivers and got most of the way through writing functions to enable data logging and transmission over 2.4GHz radio. There are two main bits of functionality added, the first being centered around the WriteFullDataPacket. This function writes all accumulated data from sensors to the flash memory periodically (currently at 10Hz controlled by TIM2). Data is accumulated in two identical buffers which operate in a 'ping-pong' fashion. Buffer A is filled initially with all data until the periodic write is triggered, at which point everything accumulated in buffer A is written to flash while all new data is accumulated in buffer B. On the next write the opposite happens, with buffer B being written to memory while data accumulation switches back to buffer A. While all functions are currently blocking for testing simplicity, in the future data collection will be among the highest priority tasks and so may take place in the middle of a write. This method prevents new data being written into the buffer currently being committed to flash which could cause data loss. Data accumulation into the buffers is handled by 'AppendLogPacket' functions specific to each sensor, which handles packaging their data into byte arrays and appending them to the buffer.

The second main bit of functionality is the data transmission. There is no USB or UART connection on this board currently so I plan to use the LAMBDA80 module to transmit the stored data to a host PC over 2.4GHz radio. While this will take longer than a wired connection, using the highest data rate modulation settings makes the expected transfer times manageable, though wireless transmission is more error prone and so will require error correction mechanisms. I have currently implemented a very simple function which reads all flight data and transmits it half a page at a time in blocking mode. To facilitate this, I added counters for the number of bytes and packets contained in the data section of flash which are initialised and maintained by the driver. There is currently no packet checking for error correction and only the transmit side is implemented.

I also finally got the desoldering iron I ordered and was able to switch the LAMBDA modules into their correct places using it, meaning I can now begin testing the LAMBDA drivers. First though, I need to make some 2.4GHz antennas (likely a ground plane monopole design like the 868MHz ones) and make a receiver device that can pass the data to the host PC. I plan to do this using the stm32 nucleo-g431kb boards I got a while ago and some simple breadboard circuitry so that I can get it up and running ASAP.

---
### Apr 29th 2026

Over the past few days I've been working on integrating the two LoRa transceivers. I soldered the LAMBDA62 and LAMBDA80 modules to the board only to realise I accidentally placed them the wrong way around. Although they have the same general pin layout, the LAMBDA62 has an additional two lines for the RX and TX switch pins so to be fully operational without bodge wires I need to swap them back. I tried desoldering them with solder wick but I cannot get enough of the solder out the through holes to lift them off safely. I have ordered a desoldering pump to help with this.

In the mean time I've made a start on the software side writing basic drivers to test both modules, starting with the LAMBDA62. At the moment I have written functions to do all needed functions like transmitting packets, receiving packets, and emitting a constant wave. These are all written as simple blocking functions currently for ease of testing but later they will be modified to be real time compatable by using DMA for the large buffer SPI transfers and EXTI interrupts on the BUSY pin to replace the current blocking polling loops. EXTI interrupts will also be used for the DIO pins to notify the MCU on packet transmission/reception. Unfortunately, DIO1 for the SX1262 (LAMBDA62) is unavailable as an EXTI interrupt as the LSM6DSR uses pin 4 as it's data ready interrupt. I didn't realise at the time of designing the PCB that EXTI interrupts cannot share pin numbers despite being in different ports. However, for the intended purpouse of simply sending a constant wave, the SX1262 does not need this second interrupt line.

I am currently in the process of writing the LAMBDA80 driver, which will use mostly the same code as the LAMBDA62 driver, just adapted to the specifics of the SX1280 instead. Once I can desolder and swap the modules I will be able to test the drivers proerly, although I will need to make 2.4GHz antennas for the LAMBDA80 first.

---
### Apr 25th 2026

Today I added some more functions to test the W25Q NOR flash driver. Here is a summary of the tests.

As detailed in yesterdays log, the driver can correctly boot up, read the metadata and flight data sections, erase the old data, and write new data. It also correctly handles wear levelling by incrementing the metadata and flight data section addresses on each write cycle.

Next I tested the bad block scanning function. It was able to complete the scan successfully and found no bad blocks as expected from a lightly used NOR flash chip.

Since there are no actual bad blocks, I expanded the bad block test to inject a fake bad block flag for the block starting at address 0x20000 (the 3rd block) and test writing and reading back a ~200KB chunk of data. The test wipes the first 10 blocks of flash before starting (to avoid a lengthy full chip wipe) which removes the existing metadata and data sections and causes blank ones to be created. This yields a repeatable setup where the metadata sector spans addresses 0x10000 to 0x11000, the bad block spans 0x20000 to 0x30000, and the data section starts at 0x1000 (starting empty). The test then writes approximately 200KB of data which, if correctly written, should expand the data section to place it's end address at 0x3FF8B. When the test was executed this exact behaviour was observed, confirming the writes were handled correctly and skipped the metadata section and bad block. Next the data was read back, starting from address 0x1000 and reading a length of 200KB. The data readout showed the data was written perfectly, with byte order being preserved across skipped sections and across pages. An additional initialisation test performed directly after this test where the chip is booted and reads the metadata/data sections confirmed it was able to read this written data perfectly from a fresh boot as well. See the test logs [here](dev_board_planning/W25Q%20bad%20block%20test%20log.txt).

Finally, I tested the wraparound behaviour at the end of memory. For this I wrote a function which initialised an empty metadata and data section by wiping existing data and then moved the empty data section start and end addresses to the last sector address in memory (0x1FFF000). It then writes 25 pages of data and reads it back from the starting address. This first test confirmed both the write and read functions correctly handle wraparound behaviour at the end of memory, perfectly preserving bytes across the transition. I then modified the test to move the data section back 1 block and inject a fake bad block in the last block, to test whether it could handle skipping a section and wrapping around at the same time. This second test worked perfectly as well. The third and final test just involved moving the data section to the original last sector address, which is now inside the fake bad block. Again, this was handled perfectly, with data being immediately wrapped around and written to the start of memory. See the test logs [here](dev_board_planning/W25Q%20wraparound%20test%20log.txt).

These tests confirm my W25Q driver is working as expected and I can now move on to the next steps, which I think will be adding in the final pieces of the board, the LoRa transceivers, to enable a command link and transfer of data.

---
### Apr 24th 2026

Finished implementing the rest of the functions needed for the NOR flash driver. These include:
- Read volume functions to read blocks of data in pages. The safe version also respects bad blocks and metadata sections and wraps the address if it extends beyond the end of memory.
- Split the safe address functions into 3 more specialised and robust functions which handle write addresses, full read addresses, and offset read addresses (for skipping around the data section only reading headers).
- Erase functions to erase either the full chip or specific blocks or sectors.
- Function which erases previously written flight data and automatically increments the data section start address and updates the metadata section.
- Function which detects and records bad blocks by writing a specific pattern to each page of memory and checking for readback errors.

I also wrote a small test function to check the W25Q is working correctly. It checks initialisation, erasing data, writing a test packet, and appending to already written data with another test packet. The first test using this function seemed to work perfectly, with all tests passing, however, when relaunching the debug session to check for correct incrementing of metadata and data addresses I encountered unexpected behaviours. At first every test after the first completely failed as the metadata section could not be found. Stepping through debug mode revealed the rx buffer was reading all zeroes on each block start address. The cause of this was eventually identified to be likely because of the erase sector and erase block functions not working correctly. Only the command was being sent, omitting the address to erase which would cause the command to be dropped or potentially cause other strange behaviour. After fixing this the data was able to be read normally.

The tests passed on each restart of the debug session now but the address incrementing was abnormal. Based on the data logging architecture we would expect the metadata address to increment by 1 block length each cycle and the data address to increment by 1 sector each cycle, except for the first cycle after a full erasure (as the empty data section would cancel the call to EraseFlightData and prevent address incrementing). In this case though, the first test after a full erase was normal, the second test showed the metadata and data start addresses did not change from the first test, and the third and fourth tests showed each address incremented twice the expected amount. Eventually I realised this was due to the slight delay in restarting a debug session allowing the MCU to boot and start executing code independently of the debug session. This caused the erase code to run at the start of the second test, meaning the addresses did not increment as expected. Then in the third and fourth tests the initialisation cycle was completed twice, once befor the debug sessions started and once after, causing the double increment. This has been temporarily dealt with by adding a 2s delay at the start of the main loop to prevent code from executing in the window between debug sessions. After adding the delay the addresses increment as normal and all tests pass perfectly.

The next priority is to test the bad block management and writing longer volumes which span multiple pages and stretch across block and memory boundaries.

---
### Apr 22nd 2026

Started developing driver firmware for data logging on the NOR flash chip (W25Q256JVEIQ). The data logging architecture plan can be seen [here](dev_board_planning/Data%20logging%20architecture.txt) which implements wear levelling and bad block management while clearing the way for fast data logging during flight where performance is critical. So far I have been working mainly on the startup sequence, gathering metadata and preparing functions for writing data safely.

Functions implemented:
- Initialisation function which resets the device, checks it is responding correctly, and sets it to 4 byte addressing mode for future commands.
- Get safe address functions. Perform checks to ensure all data is only written to a valid address (i.e. within memory bounds, not in bad blocks, (for non-metadata) not in the metadata or data sections).
- Read metadata function. Automatically scans the entire address space to find any existing metadata sectors. If found then it parses the information contained within to find the start address of the data section as well as any saved bad blocks. If not found then it automatically creates a blank metadata section at the beginning of memory.
- Write metadata function. Finds the first valid metadata sector address and writes current metadata to that sector. Optionally erases the previous metadata sector first.
- Write volume and page program functions. Work together to enable safe writing of large contiguous blocks of data only to safe addresses. Performs checks and automatically skips bad blocks and already written sections. Also splits the input data into chunks to fit within each page boundary safely.

To be implemented next:
- Functions to read volumes of data
- Functions to erase sections or the entire chip
- Function to scan for bad blocks
- Reconfigure initialisation sequence to properly use the above functions according to the [data logging plan](dev_board_planning/Data%20logging%20architecture.txt) (currently it just issues some basic commands)
- Implement planned read and write modes

<br>

---
### Apr 19th 2026

The 3rd board utilising the new V2 design was brought up successfully! Every important line was tested for shorts with a multimeter prior to closing the power isolation jumpers to each section one by one, all of which powered on successfully. The only section not brought up was the magnetometer/barometer section which contained a short between power and ground due to bridging under the MMC5983MA. Due to the lack of a working hot air gun firmware development was started with this section disconnected for a couple of weeks.

#### Firmware development pt.1
Initial tests using STM32CubeIDE with basic startup code showed the MCU was working perfectly and could interface with the peripheral devices like the user LED and accelerometers. The HAL library is used for functions like I2C and SPI communication to handle them robustly and get the board up and running quickly. Currently all communications operate in blocking mode for testing but this will be changed to use non-blocking DMA when moving to an RTOS architecture.

I started by writing drivers to handle the LSM6DSR and ADXL375 accelerometers, both on SPI bus 1. Both are set to sample measurements at 100Hz and send interrupts when their FIFO buffers contain a configurable number of measurements (currently 4). These trigger EXTI interrupts which set a 'data ready' flag and cause the MCU to initiate reading from the FIFO in the next loop. Data from the FIFO is read and the raw bits are converted into readable measurements and stored in buffers which are overwritten each time a new set of measurements comes in.

Before I could develop drivers for the other sensors (GPS, barometer, magnetometer) I had to fix the solder bridging under the MMC as it not only created a dangerous short between power and ground, meaning I couldn't power the magnetometer and barometer, but it also shorted the I2C bus SDA and SCL lines, meaning the GPS on the same bus could not be used.

#### Repairing the MMC
Eventually I got my hot air gun working again and attempted to repair the MMC. I tried applying some flux paste and reflowing with the hot air gun without lifting the chip off first but after a while of heating this did not resolve the bridges. I then tried removing the chip, wicking the pads on the PCB and chip flat, applying a small layer of solder on the PCB pads, and then reflowing the solder with flux while the chip sat on top. This did resolve the bridges and solder the chip properly but the MMC was unresponsive to an I2C scanner or direct I2C communication attempts. I now realise this is likely due to the extreme heat applied to it by prolongued hot air gun heating and wicking the pads with a soldering iron. A second attempt to transplant the MMC from the first PCB attempt (to which power was never applied) also ended identically. The chip soldered well but failed to respond likely again due to extended hot air exposure at temperatures too high. I attempted to solder a third fresh MMC to the board, this time trying to be more cautious with hot air exposure, but it also ended the same way.

It was at this point I realised that too much heat exposure must be the issue. The PCB schematic looked good after triple checking it and the soldering seemed to be working ok, not causing any bridges and soldering the pads properly (checked by testing the input diodes on the pins). I performed a series of thermal tests to identify the most conservative possible hot air conditions I could use to solder the chip from the underside of the PCB to avoid direct hot air exposure (see [thermal tests](../hardware/avionics/avionics_dev_board/Hot%20air%20tests.md)), and switched to using leaded solder to reduce the melting temperature needed. After soldering another fresh MMC using the newly identified more conservative conditions and verifying no shorts were present the board was powered on and the MMC responded to I2C calls! Subsequent software testing revealed that the SET/RESET function of the MMC does not seem to be working so more testing needs to be done to figure out why. The CAP pad may not have soldered correctly for example. This is non essential for the function of the MMC though as a different and more robust reading calibration method will eventually be implemented.

#### Firmware development pt.2
After successful repair of the MMC I was able to develop drivers for all remaining sensors, all of which use the same I2C bus as they are all slower sensors operating at 10Hz. Apart from the MMC SET/RESET issues mentioned above driver development for all these sensors went very smoothly and they all seem to work just fine. I have not been able to fully test the GPS module yet however as testing the board indoors prevents it from acquiring a satellite lock. It does output valid empty NMEA sentences however, so it seems to be working. To fully test it I will need to implement data logging and take it outside.

#### Data logging
Currently I am working on writing a driver for the NOR flash chip to enable data logging and readback. I have implemented a startup function and am currently trying to figure out a good structure to store the data efficiently and robustly. Below is my current plan for storing the data:

Buffers fill up with raw data that has been collected since the last write. Data is logged at 10Hz, at which point whatever is in the buffers is concatenated into a 'packet' that is sent to be written to storage. Each packet has a packet header with a sync word and information about the contents of the packet, followed by each piece of data which have their own headers containing information on the size and type of data they represent.

**Packet structure:**
\>> 4 Byte start sync word (AABBBBAA)
\>> 4 byte header: Total number of readings in packet [31:24], Total number of bytes in packet [23:8], Checksum [7:0]
[[[
\>> 2 byte header: Data type [15:12], Total number of bytes in data [11:0]
\>> Raw data (variable length)
]]] x N

### Note on updates going forward
From now on I am going to try and write these updates more informally and more fequently, almost for every day I work on something ideally. This will mean the updates will be smaller but overall contain much more detail as I will be able to accurately describe everything I've done and the decisions made, which become more difficult to remember after a while. It also reduces the friction to writing these updates which has been a problem. I hope that writing more frequent updates will also serve as a better look into the process, rather than just the results, of this project which I (and hopefully others) can look back on later.

---

### Apr 1st 2026

Further testing of the second avionics dev board ultimately seemed to suggest the board had some sort of catastrophic failure which has now left it unrepairable. Thermal imaging while powering the board bypassing the buck converter using a current limited benchtop power supply set at 500mA showed uniform heating across multiple components (the MCU, GPS module, accelerometers etc.). The amount of heating rose proportionally with the current limit set on the power supply.

#### Thermal imaging of the avionics dev board over time

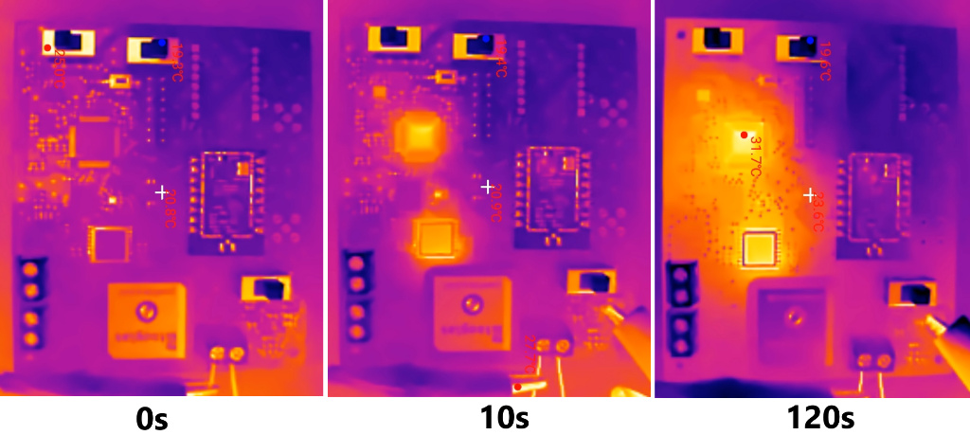
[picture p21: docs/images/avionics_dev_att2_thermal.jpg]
Thermal imaging of the avionics dev board over time


Additionally, attempts to find any dead shorts by measuring the voltage drop between GND and various points around the board gave uniform readings for every point tested. Due to the lack of power isolation mechanisms on the board it was not possible to disconnect sections of the board to test individually, however, after desoldering the inductor in the voltage regulator section to isolate the buck converter from the rest of the board I was able to measure dead shorts on both sides. These tests point towards the chips on the board having been damaged by an overvoltage event during the initial power up, potentially caused by a poorly soldered or dysfunctional buck converter outputting too much voltage.

<br>

### Avionics dev board V2

To prevent the next board facing the same fate I decided to redesign some parts of the board to improve the bring up phase and testability, as well as adding some extral QoL things. The second version of the avionics dev board includes the following changes from V1:

- Changed SWD interface pins to STDC14 form factor
- Added a user LED and button to the free MCU pins
- Added solid ground and power test points in the middle of the board
- Add jumpers to isolate power to the main power rail and to individual sections of the board
- Switched to using smaller buttons to save space
- Increased distance between headers for the LAMBDA modules as they use non-standard spacing
- Switched to a lower 500mA but slower blowing fuse to prevent potential issues with inrush current
- Rearranged the fuse to be the first component after the power switch
- Decreased resistor values on LEDs from 1kR to 220R

#### Full board view (red = top signal layer, blue = bottom signal layer)

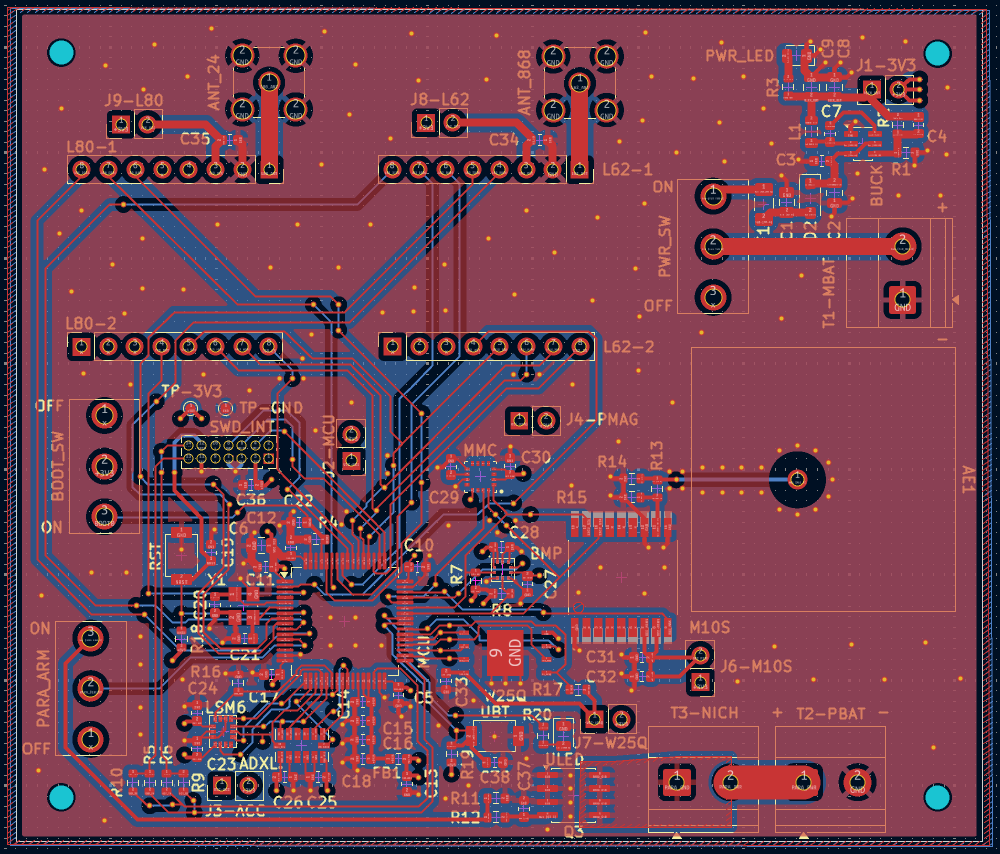
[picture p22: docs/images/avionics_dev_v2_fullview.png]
Full view of avionics dev board v2


The new PCB design and fresh components were ordered and I have begun assembling the board. I am only assembling components as and when they are required this time to prevent any unneccesary damage if something goes wrong again. So far, all SMD components were soldered via hotplate reflow as before, and the main power terminal, power isolation jumpers, and switches were soldered manually. Extra care was taken to not apply too much solder paste as this may have caused the issues seen in the second attempt of V1. A few minor bridges between MCU and buck converter pins were resolved after reflow though there is still some potential bridging under the MMC magnetometer module which is difficult to assess with my current tools. I have ordered some smaller multimeter test probes to enable easier measurements of lines connecting to the MMC module to help diagnose any potential issues before bringing up the board completely.

Before the potential MMC bridging is resolved though I tested the power regulator section of the board by disconnecting all power isolation jumpers, ensuring the regulator did not connect at all to the rest of the board. First I probed all the pins of the buck converter to ensure there were no shorts and they were connected properly. I also tested a few other parts for shorts and checked diode orientation and fuse continuity. All of these tests passed. Then for an initial test to ensure the buck converter worked safely I used a benchtop power supply to supply 9V at a low current limit of 35mA. When this power was supplied, the buck converter output a stable 3.3V and thermal imaging confirmed no components were heating up substantially.

I next plan to use the multimeter to thoroughly test and resolve any issues with the rest of the board before bringing up each section individually.

---

### Mar 10th 2026

The PCB and components arrived and I was able to assemble the PCB using hotplate reflow. The first attempt went well except for a misaligned MCU which meant each pin in one axis was offset by 1. I tried to correct this by using a hot air station to move the MCU but it seemed to be not heating it well enough to melt the solder. I now know I should have used the hot air station while the board was soaking in 150C heat on the hotplate. Instead I tried using a soldering iron to melt the solder and move the MCU but this resulted in many of the pins being bent beyond repair.

Luckily I had bought two sets of every component for exactly this scenario so I attempted it again the next day. This time making sure the MCU and all other components were more precisely aligned. After reflow all components appeared to be correctly aligned and a few minor bridges between MCU and sensor pins were corrected using the soldering iron. Through hole components were added on to complete the board.

After assembly the board was tested with a fresh 9V battery. Upon flipping the power switch on I saw what looked like a brief flash of light in the voltage regulator area and no light from the power LED. Testing with a multimeter revealed the 1A fuse just before the buck regulator had blown and further testing revealed a short circuit is present between ground and power somewhere on the board. In order to locate the short circuit I have ordered a benchtop power supply and thermal camera to pump a limited current into the circuit and observe hotspots.

#### Assembled dev board in it's current state

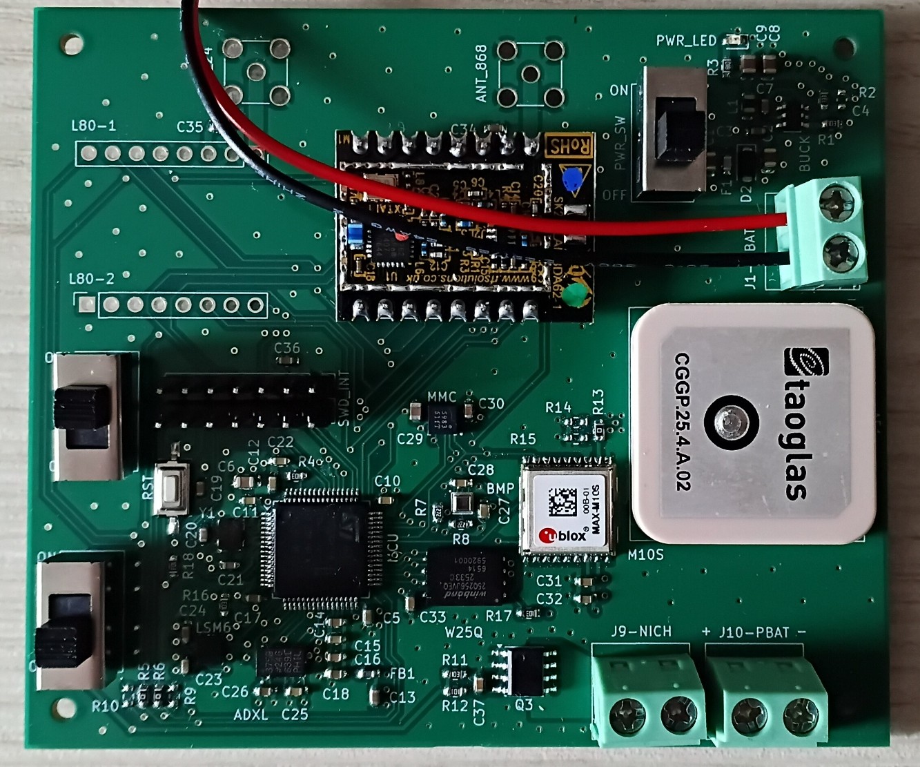
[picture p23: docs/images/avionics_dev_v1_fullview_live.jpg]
Full view of avionics dev board v1 assembled


---

### Feb 28th 2026

While waiting for components to arrive I've been learning about the general STM32 MCU startup process and writing some very simple bare metal startup code for the STM32G431KB MCU. This is able to be flashed onto the STM32G431KB-NUCLEO board and the loop counter can be seen increasing using GDB and OpenOCD.

---

### Feb 12th 2026

First design interation of the avionics development PCB has been completed. The PCB and components have been ordered and I will begin assembly and testing when they arrive.

#### Full board view (red = top signal layer, blue = bottom signal layer)

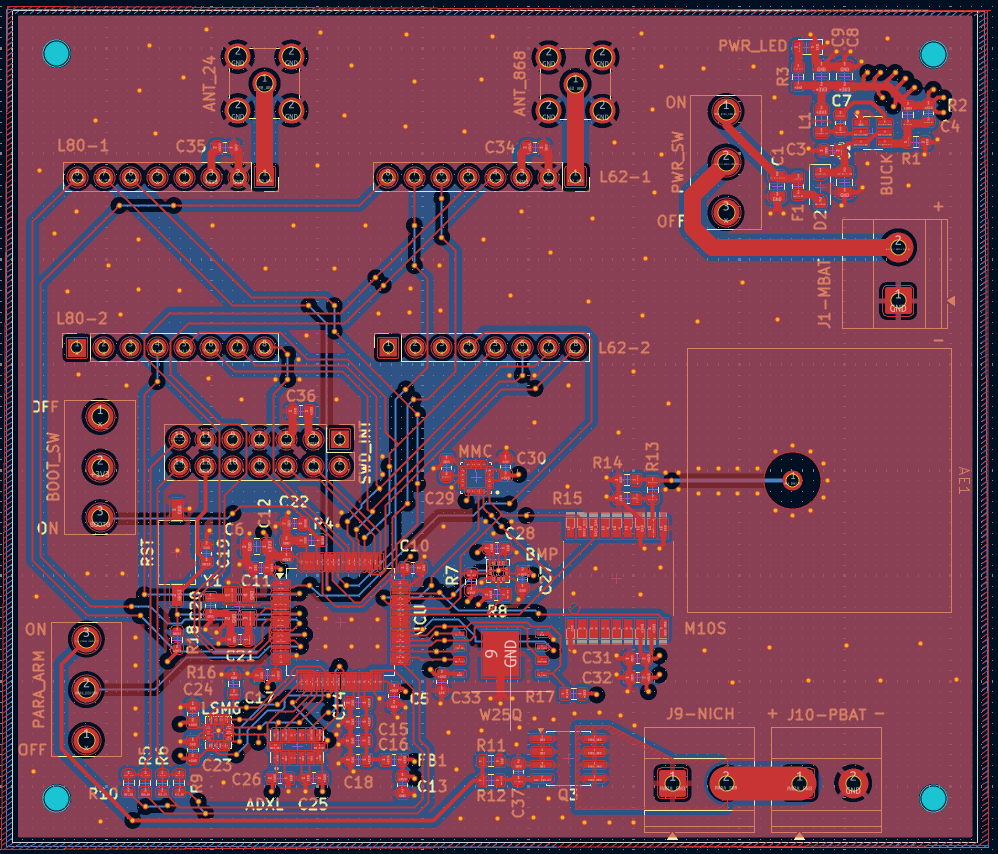
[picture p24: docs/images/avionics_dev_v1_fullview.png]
Full view of avionics dev board v1


The board is organised roughly into 5 sections:
- Top right: Power supply and voltage regulator. Power is supplied by a 9V battery across the J1 terminal and stepped down to 3V3 by a TPS563201 buck converter.
- Top middle/left: LoRa transceivers and antenna SMA connections.
- Middle right: GPS module and antenna.
- Bottom right: Parachute deployment system. Utilises a separate power supply driven by a MOSFET to burn a length of nichrome wire.
- Bottom left: Main MCU and sensor block.

This board uses a 4 layer stackup of SIG-GND-PWR-SIG, enabling easy distribution of power throughout the board. To minimise return path issues, only not critical signals are routed on the bottom signal layer with the power layer as it's reference. The only signal this was not possible for is the GPS antenna line, for which a separate island was made on the power layer surrounding the trace tightly coupled to ground using many vias. Along with this, 4 vias were placed to surround the signal via when it transitions back up to the top layer to ensure it always maintains a close ground reference.

#### GPS antenna trace shielding

GPS antenna trace shielding

0602 footprints were used for most passives except large value capacitors. I plan to assemble the board using a stencil to apply solder paste and a hot plate to reflow. Through hole components can then be soldered manually afterwards.

---

### Feb 1st 2026

The issue causing miscounting of packet sequence numbers by the receiver in the LAMBDA62 rangetest setup has been identified and fixed. Testing confirmed this was caused by the transmitter repeatedly resetting and starting the transmission counter from 0 again. The 9V battery powering the transmitter was outputting a much lower voltage than expected (around 7V, while the receiver battery output almost 9V) so a fresh battery was used. This fixed the issue and transmission was able to continue uninterrupted while the receiver correctly counted each packet. To mitigate the chance of this issue happening in the field spare batteries will be brought.

Component selections for the avionics unit have been finalised. Changes from the previous selections are detailed below:

- MCU = STM32G474RET6; The chip will be used rather than a nucleo board for compactness and to reduce cost.
- Storage = W25Q256JVEIQ; NOR flash will be used instead of NAND flash to increase reliability for storing critical flight data. This still offers more than enough storage capacity to write flight data for multiple long launches if needed.
- IMU = LSM6DSR; Switched to the R variant for lower risk of gyro saturation for negligible increase in cost.
- Pressure/temp = BMP581; Mainly due to lack of availability of the BMP390, but also slightly increased sensitivity.
- Magnetometer = MMC5983MA; Highly improved performance with degaussing option to remove offsets caused by other nearby components.

---

### Jan 28th 2026

Started designing the development PCB for the avionics unit, beginning with the power source. This utilises a TPS563201 buck converter to provide a stable 3.3V DC source from a 4.5V-17V input. Component values were taken from the datasheet specifications with resistor R2 being 33kΩ to get a 3.3V output. A space for capacitor C4 was added despite likely being unneeded so that the pads are there for easy addition later if testing shows it is needed. A switch was also added between the positive terminal input and the TPS563201 enable pin to allow the power source to be easily switched on and off. Temporary footprints have been used for the moment until actual component models are decided.

#### Schematic view

Avionics dev board schematic view

#### PCB view

Avionics dev board PCB view

#### 3D view

Avionics dev board 3D view

---

### Dec 2025 - Jan 2026

This is a summary of the progress made in the first couple months of the project before I started taking logging more seriously.

I started the project by making prototype breadboard circuits to test communication between two LAMBDA62 modules, which contain the SX1262 868MHz transceivers used for this project. Arduino nanos were used to drive the transceivers through TXS0108E bidirectional logic level shifters to match the 5V Arduino logic to the 3.3V logic of the LAMBDA62 module. See the below [wiring schematic](../hardware/prototyping/LAMBDA62_rangetest/RangeTest.kicad_sch) and photo of the assembled rig.

#### Wiring schematic

LAMBDA62 range test wiring schematic

#### Assembled test rig

LAMBDA62 range test setup

The antenna was an 868MHz ground plane monopole made from 1mm diameter bare copper wire soldered onto a SMA female panel mount connector. The monopole was originally cut to be 90mm long while the radials were cut to extend 100mm from the edge of the panel mount. A nanoVNA was used to tune the antenna by cutting the monopole until the point of minimum SWR was close to 868MHz. The final antenna and nanoVNA test results are shown below.

#### Final antenna

868MHz ground plane monopole

#### NanoVNA test results

868MHz monopole nanoVNA test results

<br>

A simple lightweight Arduino sketch ([LAMBDA62_rangetest.ino](../firmware/prototyping/LAMBDA62_rangetest/LAMBDA62_rangetest.ino)) was made to drive the LAMBDA62 using only the SPI library. This sketch can be uploaded to the transmitter and receiver by changing the 'receiver' variable at the top. The transmitter will transmit the payload at the soonest avaiable opportunity with a 20ms delay in between packets and the receiver will receive each packet and determine whether it was sent correctly, along with measuring the strength of the signal. This information is output through the serial port of the Arduino to a connected computer running the [SerialMonitor.py](../firmware/prototyping/LAMBDA62_rangetest/SerialMonitor.py) script, which parses the information and outputs summary statistics every 50 packets to the command line and a text file while writing individual packet statistics to a .csv file.

A range test was conducted on a long flat beach using this setup. The transmitter was stationary on a plastic cutting board on the ground while the receiver was moved away as it received packets. The results can be found [here](./initial_range_tests/01-01-26_results/) graphs of the per packet RSSI/SNR over time and SNR vs RSSI are below. The results were much worse than expected as packets began being missed after only 200m of distance, and all reception was lost after ~600m. However, it is very likely this was caused by bad testing conditions. Placing the transmitter on the ground likely greatly reduced signal transmission efficiency due to ground proximity effects. The weather was very windy which meant the transmitter had to be touched for a significant portion of the test, likely also reducing the antennas radiation effectiveness due to body coupling. In addition, the receiver was moved by holding the breadboard it was attached to and letting it hang underneath held by the coax cable. Walking motions and the wind therefore cause significant polarisation mismatch as the receiver swung around. Another issue encountered during the test was the miscounting of packet sequence numbers by the receiver, causing the missed packet calculations to be significantly off. This issue was not observed during testing before the range test. The issue may have been caused by the receiver not correctly detecting packets with CRC errors, resulting in wrong data being decoded for the sequence number which then throws the calculations off. This was not tested before the first range test as I had no reliable way to induce CRC errors.

#### Per packet RSSI and SNR over time

Per packet RSSI and SNR over time

#### Per packet SNR vs RSSI

Per packet SNR vs RSSI

Although noisy and less than ideal, the SNR vs RSSI relationship shows promise for the feasibility of using the AD8302 module with 20-30dB gain LNAs for PDOA tracking. The SNR does not begin appreciably dropping until an RSSI of around -90dBm, which shows the 868MHz signal is still received significantly above the noise floor in the RSSI range of the AD8302 (-60dBm) + 20-30dB LNA (-90dBm). Therefore it should be able to reliably process the CW tone uncomplicated by noise until its strength falls out of range.

To ensure the next range test provides more useful results the following modifications will be made:
- Fix the packet sequence number bug which is potentially caused by incorrect handling of erroneous packets. Test this by inducing corrupted packets, potentially by using an implicit/explicit header mismatch between the transmitter and receiver.
- Make a testing enclosure to protect and hold the components in place more rigidly. This will help protect the electronics from outside conditions and hold the antenna in place on an insulating material to ensure a better polarisation match. Additionally, they can be held high off the ground using handle underneath to reduce ground and body coupling effects.

The testing enclosure has been modeled and 3D printed with PETG (see model files [here](../mechanical/simple_range_test/) and images below).

#### Range test enclosure (closed - handle on the left screws into the base)

Range test enclosure closed

#### Range test enclosure (open)

Range test enclosure open

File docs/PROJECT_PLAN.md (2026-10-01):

# **Avionics project plan**

Overall plan for the project and a rough order for the development timeline. Updated 01/07/26.

## **Project overview**

Sensors on a model rocket collect readings and a microcontroller integrates them in real time to calculate stats like position and velocity. The full dataset is written to non-volatile storage and a subset of important info is transmitted over the air to a ground station.

The ground station uses the received position and velocity data to calculate the expected angle the antenna array needs to rotate to keep pointing at the rocket. An array of 3 ground nodes will also periodically measure their distance to the rocket and transmit the results to the controlling node connected to a PC. These ranging results, along with known distances between each node, can be used to get a second measurement of the position of the rocket which is completely independent of the onboard sensors. These two methods allow the ground station to update the current position of the rocket and rotate the antennas to track it in real time.

The ground station receives the main telemetry data via a high gain central antenna and decodes and passes this info to the connected computer (the ‘control center’) which displays the info on a live updating GUI. This control center is also connected to the launch pad to initiate the launch, along with being able to control the ground station nodes and rocket by issuing commands (e.g. to calibrate sensors before launch). Each network node and the rocket has an 868MHz and 2.4GHz transceiver integrated. The 868MHz band is used to transmit commands while the 2.4GHz band is used for ranging and transmitting larger data streams.

```mermaid
---
config:
  theme: neo-dark
  layout: dagre
---
flowchart TB
 subgraph Rocket["Avionics Unit"]
        MCU_R["MCU<br>STM32G474"]
        Sensors["Sensors<br>IMU, GPS, Baro"]
        NOR["NOR flash"]
        RKT_24["SX1280 2.4GHz"]
        RKT_868["SX1262 868MHz"]
        Parachute["Parachute<br>deployment"]
  end
 subgraph Air["Ground station (controller)"]
        GS_24["SX1280 2.4GHz"]
        GS_PDOA@{ label: "<span style=\"padding-left:\">SX1262 868MHz</span>" }
        MCU_G@{ label: "MCU<span style=\"padding-left:\"><br>STM32G474</span>" }
        Motors["Stepper/Servo<br>tracker base"]
        GUI["Qt GUI<br>Data display and<br> mission control"]
  end
 subgraph s1["Ground station (ranging nodes x2)"]
        n1["SX1280 2.4GHz<br>Ranging"]
        n2@{ label: "<span style=\"padding-left:\">SX1262 868MHz</span>" }
        n3@{ label: "MCU<span style=\"padding-left:\"><br>STM32G474</span>" }
  end
    Sensors -- SPI/I2C --> MCU_R
    MCU_R -- SPI --> RKT_868 & NOR
    MCU_R <-- SPI --> RKT_24
    MCU_R -- GPIO --> Parachute
    RKT_24 -. Telemetry .-> GS_24
    RKT_868 <-. Cmd .-> GS_PDOA
    GS_24 <-- SPI --> MCU_G
    GS_PDOA <-- SPI --> MCU_G
    MCU_G -- GPIO/PWM --> Motors
    MCU_G <-. USB .-> GUI
    GS_24 <-. Ranging .-> RKT_24
    n1 <-- SPI --> n3
    n2 <-- SPI --> n3
    n2 <-. Cmd .-> GS_PDOA

    GS_PDOA@{ shape: rect}
    MCU_G@{ shape: rect}
    n1@{ shape: rect}
    n2@{ shape: rect}
    n3@{ shape: rect}
```

### **Onboard avionics**

The rocket will have an onboard avionics unit containing multiple sensors, transceivers, antennas, a parachute system, and a central MCU. Specific models below:

* MCU = STM32G474RET6

* NOR flash = W25Q256JVEIQ

* IMU = LSM6DSR

* High range accelerometer = ADXL375BCCZ

* Pressure/temperature sensor = BMP581

* Magnetometer = MMC5983MA

* GPS = MAX-M10S-00B

* 868MHz LoRa transceiver = SX1262 (LAMBDA62)

* 2.4GHz LoRa transceiver = SX1280 (LAMBDA80)

Two transceivers will be present on the rocket with their respective antennas – the SX1262 (868MHz, LAMBDA62 module), and the SX1280 (2.4GHz, LAMBDA80 module). The 868MHz band will be used to receive commands from the controlling ground station node and send back responses. The 2.4GHz band will be used to transmit telemetry data at 10Hz, as well as range with the network nodes. Transmitted data will include the rockets calculated position, velocity, acceleration, orientation, and temperature/pressure.

A central MCU (STM32G474RET6) will be used to control everything in the avionics unit. It will:

* Interface with the sensors and collect data from them.

* Write the raw data to a NOR flash chip (W25Q256JVEIQ) for later in-depth analysis.

* Integrate the raw data into accurate estimates of position (IMU, GPS), angle (IMU, magnetometer) etc.

* Interface with the two transceivers to process commands and send out telemetry data periodically.

* Activate the parachute deployment system when necessary.

FreeRTOS will be implemented to handle all these tasks concurrently.

<br>

### **Ground station**

The ground station is made up of a network of 3 nodes, two ranging nodes and a main controlling node. The controlling node is connected to the control center PC via USB and will use a central 2.4GHz high gain directional antenna and an omnidirectional 868MHz antenna. The 2.4GHz antenna will likely be either a Yagi with many elements or a dish, while the 868MHz antenna will likely be a sleeve dipole. The 2.4GHz antenna will be mounted on a motorised base that allows it to point towards any location in the sky. Azimuth will be controlled by a stepper motor to allow 360-degree movement, while elevation will be controlled by a servo motor. The MCU will use telemetry transmissions received on 2.4GHz and ranging information received on 868MHz to track the rocket as it moves. The MCU also passes all of this information on to the control center.

The ranging nodes are simpler and will use omnidirectional 2.4GHz and 868MHz antennas. They will be placed at least a few hundred meters apart and form a triangle around the launch pad with the controlling node. These are used purely to range the rocket to provide a second position measurement and are controlled by the controlling node sending commands over 868MHz.

<br>

### **Control center**

The controlling node MCU sends all information received from the rocket to the control center computer. This info is then processed and displayed on a live updating GUI (design concept below). The GUI will show many interesting stats about the flight which are updated live. Along with this, it will also have interactable 3D renderings of the path of the rocket and it’s current orientation and movement.

The GUI will also have a built in CLI which can be used to control various functions of the ground station and rocket by issuing commands. For example, to calibrate sensors before launch, to initiate the launch itself, to start/stop data recording etc.

Control center GUI design concept

<br>

### **Ideal outcome**

Once fully built the ideal flow of a launch from start to finish is as follows:

* Set up ground station, launchpad, and control center.

* Initiate connection between control center and ground station controlling node (wired), and controlling node to rocket and ranging nodes (radio).

* Calibrate ground station and rocket sensors by issuing commands via control center CLI. These get sent to the controlling node which transmits the commands to the relevant node.

* Send command to set off rocket launch. Rocket starts telemetry transmission and periodic ranging on 2.4GHz.

* Launch pad sets off motor and rocket launches.

* As the rocket enters steep ascent telemetry packets describing its position reach the ground station which moves the motorised base to keep the rocket in view of the directional antennas.

* Telemetry data is passed to the control center which processes the data and updates the GUI live to show stats and 3D renderings of the rocket.

* The ground station integrates both telemetry and ranging measurements to track the rocket. If the ground station does not receive a valid telemetry packet at the expected interval it will update the expected position of the rocket by using the ranging results and the last correctly received position, velocity, and acceleration values to simulate it's path in between updates. This will continue until another packet is received, at which point the new position overrides any calculated position up to that point.

* As the rocket reaches its apex and begins descending the avionics unit deploys the onboard parachute.

* Rocket lands safely on the ground.

* Avionics unit detects landing and stops telemetry recording and transmission after a short delay, but continues broadcasting it's GPS positon.

* Rocket retrieved and full dataset can be downloaded from onboard storage.

<br>

## **Development timeline**

##### 1\. RF link validation and range tests

* [x] Model and 3D print antenna testing enclosures.
* [ ] Assemble SX1262 (LAMBDA62 module - 868MHz) and SX1280 (LAMBDA80 module - 2.4GHz) test rigs and perform range tests to validate feasibility and collect field data for RSSI and SNR at distance.

##### 2\. Avionics unit

* [x] Design avionics unit development PCB with convenience features like line test pads, 0 ohm resistors etc. Transceivers are used as modules plugged into the PCB (later to be soldered permanently) while everything else is used as bare chips soldered directly to the PCB via hotplate reflow. Also include power management IC and safety arming switch for parachute deployment system.
* [x] Acquire parts for avionics development PCB and assemble it. Iterate design as required.
* [x] Write sensor drivers.
* [x] Write NOR flash chip driver.
* [x] Test storage of sensor data on NOR flash.
* [x] Write SX1280 and SX1262 drivers.
* [x] Implement FreeRTOS on the MCU.
* [x] Implement tasks to collect all sensor data when ready.
* [x] Implement task to write all collected sensor data to NOR flash chip without interrupting critical sensor reading tasks.
* [x] Write and test routine for downloading data from flash storage.
* [x] Test sensor data acquisition and accuracy.
* [x] Gather field test data.
* [x] Write and test calibration routines for sensors (magnetometer and accelerometers).
* [x] Write a sensor fusion and data integration algorithm to accurately track position over time (on PC).
* [x] Implement task to do the sensor fusion and data integration algorithm on the avionics unit.
* [x] Implement task to do periodic transmission of calculated data through the SX1280.
* [x] Implement a flight stage state machine which controls which sensors to use for position tracking over time.
* [ ] Implement and test parachute deployment logic.
* [ ] Final field tests of full avionics unit.

##### 3\. Motorised antenna base

* [ ] Build motorised portion of antenna base with stepper driving azimuth and servo driving elevation (no antenna mountings yet).
* [ ] Design the controlling node PCB.
* [ ] Integrate drivers for RF and USB.
* [ ] Write drivers to drive the antenna base motors.
* [ ] Implement and test algorithm to enable the STM32 to drive the base to point at any angle in the sky.
* [ ] Upgrade algorithm to take a location and point at it by determining the relative angle.
* [ ] Build, test, and mount the 2.4GHz main telemetry antenna onto the base.
* [ ] Hook up antenna to SX1280 driven by the STM32 and test receiving of periodic telemetry transmissions from the avionics unit.
* [ ] Add calibration routine for the base to set it's initial offset from signal source.
* [ ] Test moving the antenna base to constantly point at the received location data (may be best done by mounting the avionics unit on a drone).

##### 4\. Control center

* [ ] Implement task on antenna base STM32 to periodically send relevant data to control center computer via serial connection.
* [ ] Build basic control center GUI to display received data (simulated or real) in text.
* [ ] Test GUI with fake injected data and real field data.
* [ ] Implement bidirectional communication between ground station and avionics unit through 2.4GHz.
* [ ] Implement command line into GUI to issue commands to the antenna base through serial connection.
* [ ] Expand GUI to add in 3D graphics of rockets position and orientation.
* [ ] Test all systems with fake and live data.

##### 5\. Adding ranging nodes

* [ ] Build and test the ranging node PCBs.
* [ ] Build the 2.4GHz and 868MHz antennas and test them.
* [ ] Implement all RF drivers.
* [ ] Test ranging accuracy.
* [ ] Implement a ranging network protocol and test it.
* [ ] Implement a calibration routine to allow the controlling node to accurately determine the initial distances between all nodes on the network.
* [ ] Implement an algorithm to use ranging results and calibrated initial distances to determine the rockets position.
* [ ] Integrate periodic ranging into the regular telemetry transmission task.
* [ ] Final test of ranging position tracking.

##### 6\. Rocket

* [ ] Build and test model rocket with no avionics.
* [ ] Build and test model rocket with weights equivalent to avionics.
* [ ] Design compacted avionics unit PCB which integrates any changes and removes development features.
* [ ] Integrate avionics PCB into rocket.
* [ ] Integrate and test parachute deployment.
* [ ] Final tests of full system with fake and live data.
* [ ] Launch.

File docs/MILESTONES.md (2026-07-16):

# **Milestones**

All major milestones achieved and when.

\[03/04/26] First working avionics PCB assembled.
\[26/06/26] RF controller board fully working to enable wireless command link with the avionics unit.
\[16/07/25] All sensors fully working and data is able to be downloaded off the avionics unit. First field tests to gather data.

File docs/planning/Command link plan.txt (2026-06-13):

While the LAMBDA80 is used for high bandwidth data transmission on the 2.4GHz band, the LAMBDA62 is used for transmitting and receiving command and status messages on the 868MHz band.

Because the 868MHz band will be used for bidirectional communication unlike the 2.4GHz band, it will need to account for timing collisions by using a master-slave relationship. The controller (transceiver connected to the host PC) will always initiate a communication with a specific node, and that node only can respond immediately after.

Packets will all have the following structure:
>> 3 byte header: Recipient ID [23:16], Sender ID [15:8], Sender status [7:0]
>> 1 byte message type
>> 1 byte sequence number
>> Payload (optional - variable length up to 250 bytes)

A CRC and message length are not needed as the transceivers already takes care of these in explicit header mode.

// DEVICE DISCOVERY
The controller will maintain and update a list of available nodes it can communicate with by periodically sending out device discovery packets (say every 10s when idle). These will have a recipient ID of 0xFF, which is the broadcast ID that all nodes can respond to. Any newly powered on node will default to Rx mode, and upon receiving a discovery packet will send an ACK back to the controller, at which point the list of active nodes is updated and it can be communicated with normally.

To eliminate the chance of a collision in case multiple new nodes are powered on within 10s, each node receiving a discovery packet will wait a specified amount of time before sending the ACK. The amount of time a node waits is calculated as its device ID multiplied by 50ms (e.g. device ID 3 would wait 150ms). The controller stays in Rx mode for 500ms (can be expanded later to allow more time if more nodes are added) to receive any ACKs sent in this window.

Discovery packets will have the following structure:
>> 3 byte header: Recipient ID [23:16] = 0xFF (broadcast ID), Sender ID [15:8] = 0x0 (controller ID), Sender status [7:0]
>> 1 byte message type = 0x1
>> 1 byte sequence number

ACK packets will have the following structure:
>> 3 byte header: Recipient ID [23:16] = 0x0 (controller ID), Sender ID [15:8], Sender status [7:0]
>> 1 byte message type = 0x0
>> 1 byte sequence number

// GENERAL MESSAGES
The controller must always initiate a transaction with a specific node by sending a packet with the intended recipient ID and message type fields configured. Although all nodes will receive these messages, only the node with the device ID matching the recipient ID will act on it.

All messages sent by the controller to a node must be responded to by the node with a single message within a timeout window. For simple commands this may be an empty ACK packet, or for more complex commands/status requests this can be a larger packet with a payload containing more information. If no response is received from the node within the timeout window (which is configurable based on the message type) then the controller must assume the message was lost and either try again or fall back to some other error handler.

To prevent collisions only one transaction can be ongoing at a time, and the end of a transaction is determined by the controller based on the message type and any received packets. As the 868MHz channel is intended for short, infrequent, bidirectional communication this is a reasonable restriction to impose for guaranteeing unobstructed message passing.

// GENERAL CONSIDERATIONS
To stay under the legal 1% duty cycle limit, even only using infrequent short messages, the 868MHz band will likely have to use the SX1262s FSK modem rather than LoRa. FSK should still have enough range to allow communication over hundreds of meters but allow much higher data rates to reduce the needed time on air.

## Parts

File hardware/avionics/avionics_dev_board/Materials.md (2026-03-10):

**SENSORS/ICs**
* MMC5983MA     https://www.mouser.co.uk/ProductDetail/MEMSIC/MMC5983MA?qs=B6kkDfuK7%2FD5qasHMdEt2g%3D%3D
* BMP581        https://www.mouser.co.uk/ProductDetail/Bosch-Sensortec/BMP581?qs=Li%252BoUPsLEntPL9tlFmcgXg%3D%3D
* LSM6DSRTR     https://www.mouser.co.uk/ProductDetail/STMicroelectronics/LSM6DSRTR?qs=vLWxofP3U2yp6%252BOD3KzrKQ%3D%3D
* W25Q256JVEIQ  https://www.mouser.co.uk/ProductDetail/Winbond/W25Q256JVEIQ?qs=qSfuJ%252Bfl%2Fd4o%2FNFUf7yCgA%3D%3D
* ADXL375BCCZ   https://www.lcsc.com/product-detail/C579466.html
* MAX-M10S-00B  https://www.lcsc.com/product-detail/C4153167.html
* STM32G474RET6 https://www.lcsc.com/product-detail/C521608.html?s_z=n_STM32G474RET6

**CAPACITORS:**

* 12pF   x2	https://www.mouser.co.uk/ProductDetail/Samsung-Electro-Mechanics/CL10C120JB8NNNC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
* 10nF   x2	https://www.mouser.co.uk/ProductDetail/Samsung-Electro-Mechanics/CL10B103KA8WPNC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
* 100nF  x21	https://www.mouser.co.uk/ProductDetail/Samsung-Electro-Mechanics/CL10A104KA8NNNC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
* 1uF    x5	https://www.mouser.co.uk/ProductDetail/Samsung-Electro-Mechanics/CL10B105KO8NNNC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
* 4.7uF  x1	https://www.mouser.co.uk/ProductDetail/Samsung-Electro-Mechanics/CL21A475KPFNNNE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
* 10uF   x3	https://www.mouser.co.uk/ProductDetail/Samsung-Electro-Mechanics/CL21A106KOQNNNE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
* 22uF   x2	https://www.mouser.co.uk/ProductDetail/Samsung-Electro-Mechanics/CL21A226MAYNNNE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

**RESISTORS:**

* 0      x1	https://www.mouser.co.uk/ProductDetail/YAGEO/RC0603JR-100RL?qs=sGAEpiMZZMtlubZbdhIBIFOweZSLBx1NUnQzarM2WLU%3D
* 100    x1	https://www.mouser.co.uk/ProductDetail/YAGEO/RC0603JR-13100RL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
* 1k     x1	https://www.mouser.co.uk/ProductDetail/YAGEO/RC0603FR-101KL?qs=sGAEpiMZZMtlubZbdhIBIHvQf5egq9lv5WuapZo15J4%3D
* 2.7k   x2	https://www.mouser.co.uk/ProductDetail/YAGEO/AC0603FR-102K7L?qs=sGAEpiMZZMtlubZbdhIBIMHZ5gvv1VGtHY9R6eAnJ8w%3D
* 10k    x6	https://www.mouser.co.uk/ProductDetail/YAGEO/AC0603JR-0710KL?qs=sGAEpiMZZMtlubZbdhIBIEWKOXN0akj16e5O1kzK9uk%3D
* 33k    x1	https://www.mouser.co.uk/ProductDetail/YAGEO/RC0603FR-1033KL?qs=sGAEpiMZZMtlubZbdhIBIHvQf5egq9lvh39n1j2MzKs%3D

**OTHER:**

* 2.2uH inductor         x1	https://www.mouser.co.uk/ProductDetail/TAIYO-YUDEN/LSQEA201212T2R2M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
* Sliding switch         x3 https://www.lcsc.com/product-detail/C7431054.html
* Push switch            x1 https://www.lcsc.com/product-detail/C7450623.html
* 16MHz crystal          x1	https://www.mouser.co.uk/ProductDetail/ABRACON/ABM8G-16.000MHZ-4Y-T3?qs=hxOQwdLlgerw9VxLMu5o8A%3D%3D
* N-MOSFET               x1	https://www.mouser.co.uk/ProductDetail/Diodes-Incorporated/DMG4466SSS-13?qs=sJ%252BpcIzCtBiZrDaWKxeDlA%3D%3D
* 1x2 screw terminal     x3	https://www.mouser.co.uk/ProductDetail/Phoenix-Contact/5442206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
* 1A fuse                x1	https://www.mouser.co.uk/ProductDetail/YAGEO/JB06F1001R?qs=iLKYxzqNS752SsUEEkcV%2FA%3D%3D
* Diode                  x1	https://www.mouser.co.uk/ProductDetail/Diodes-Incorporated/MBR230S1F-7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
* 120R ferrite bead      x1	https://www.mouser.co.uk/ProductDetail/TE-Connectivity-Sigma-Inductors/BMC-Q1JY0120H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
* LED                    x1	https://www.mouser.co.uk/ProductDetail/LITEON/LTST-C194KRKT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
* TPS563201DDCR          x1 https://www.mouser.co.uk/ProductDetail/Texas-Instruments/TPS563201DDCR?qs=G55MHhPmvtJ%2FRbVAaIIbqw%3D%3D
* CGGP.25.4.A.02         x1 https://www.mouser.co.uk/ProductDetail/Taoglas/CGGP.25.4.A.02?qs=QpZVHcK7GhSAV47sa7%2Fgcg%3D%3D

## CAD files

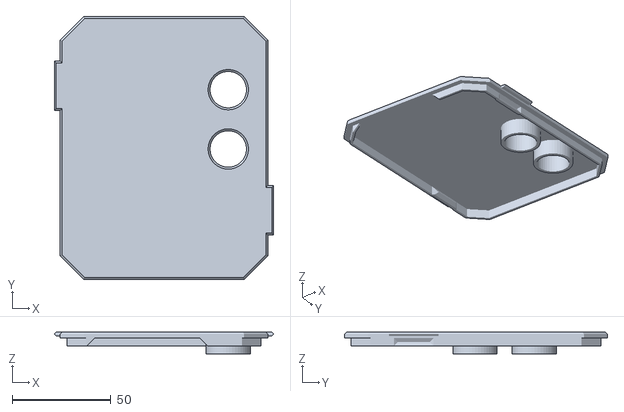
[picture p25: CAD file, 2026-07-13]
mechanical/avionics_enclosure/Enclosure lid v2.stl
111.0 x 133.0 x 11.0

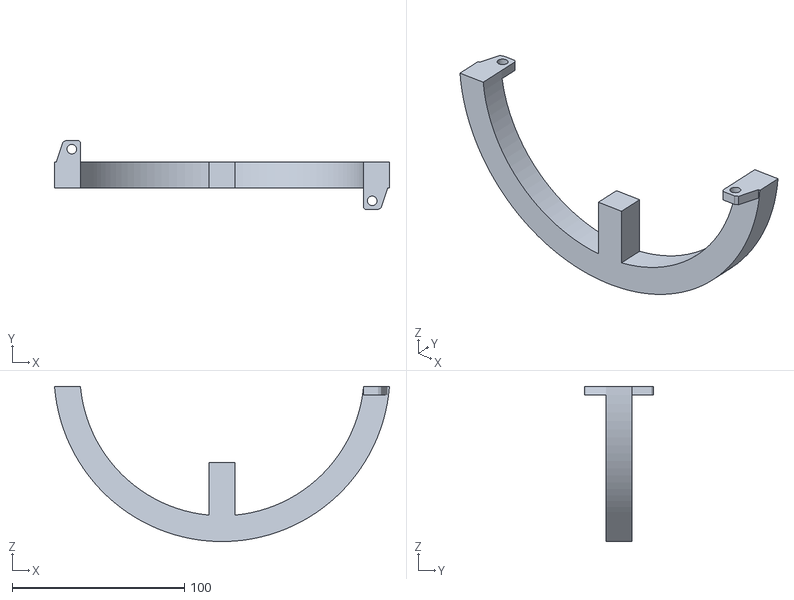
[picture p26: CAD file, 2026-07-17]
mechanical/avionics_roll_cage/Ring2.stl
194.4 x 40.0 x 90.0

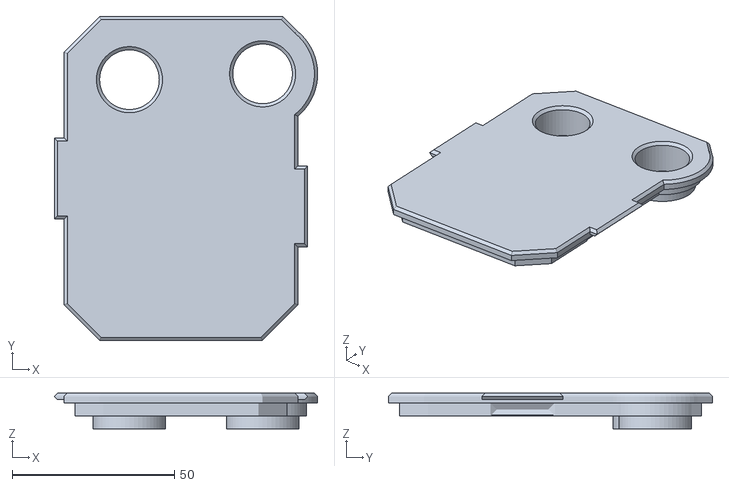
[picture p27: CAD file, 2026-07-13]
mechanical/RF_controller_enclosure/Enclosure lid v2.stl
81.3 x 100.0 x 11.0

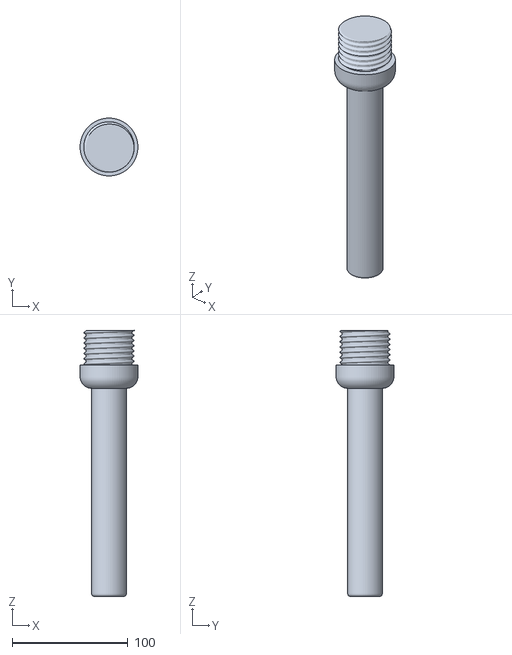
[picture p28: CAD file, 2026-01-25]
mechanical/simple_range_test/Handle.stl
50.0 x 50.0 x 230.0

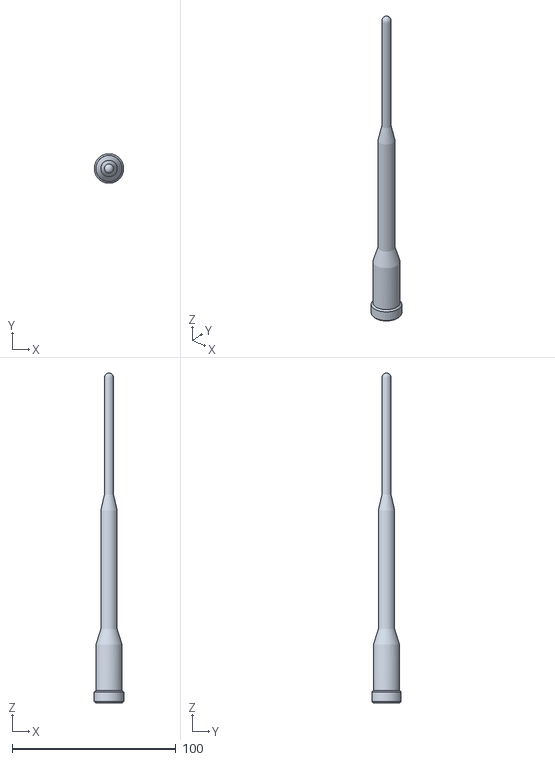
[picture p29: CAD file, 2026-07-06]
mechanical/sleeve_dipole_enclosure/body.stl
18.0 x 17.9 x 201.4

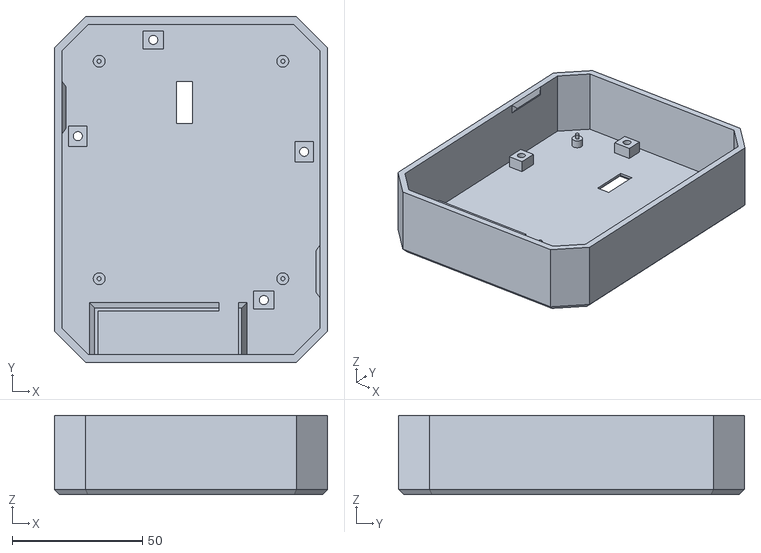
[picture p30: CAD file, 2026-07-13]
mechanical/avionics_enclosure/Enclosure body v2.stl
105.0 x 133.0 x 30.5

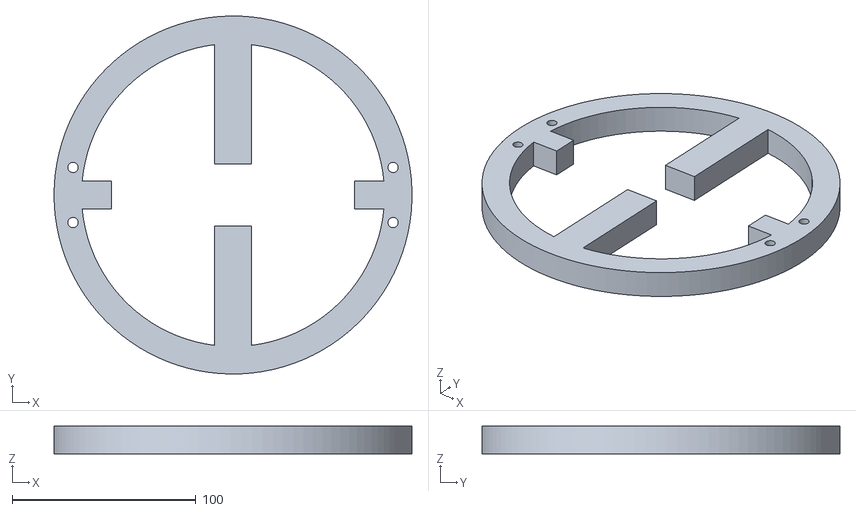
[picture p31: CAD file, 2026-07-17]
mechanical/avionics_roll_cage/Ring1.stl
195.0 x 195.0 x 15.0

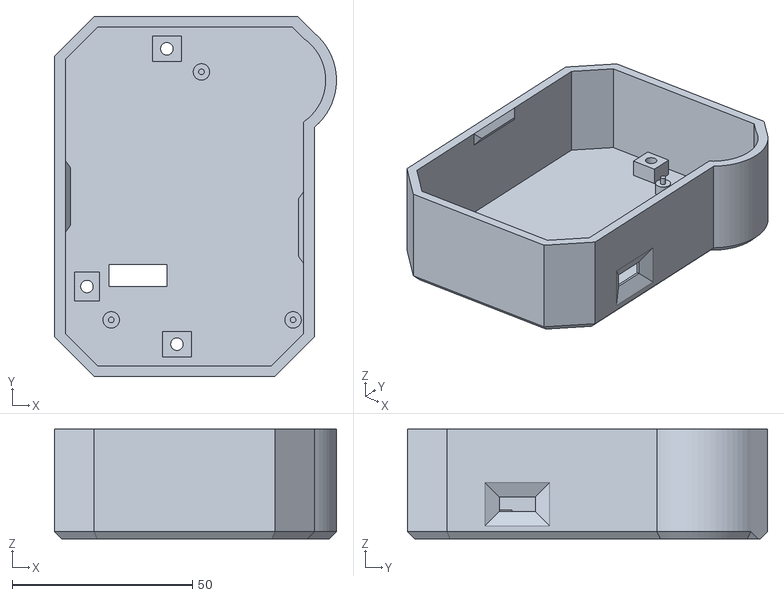
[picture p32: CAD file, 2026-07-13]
mechanical/RF_controller_enclosure/Enclosure base v2.stl
78.3 x 100.0 x 30.5

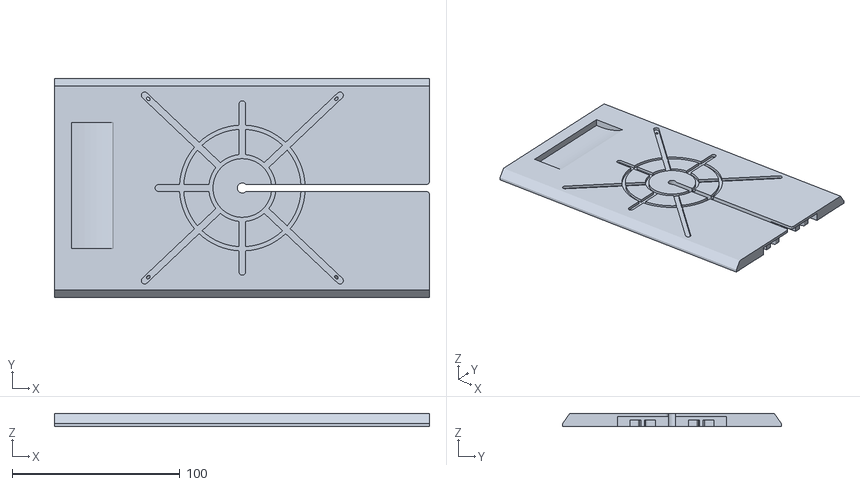
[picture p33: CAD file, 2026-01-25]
mechanical/simple_range_test/EnclosureTop.stl
223.6 x 130.4 x 8.00

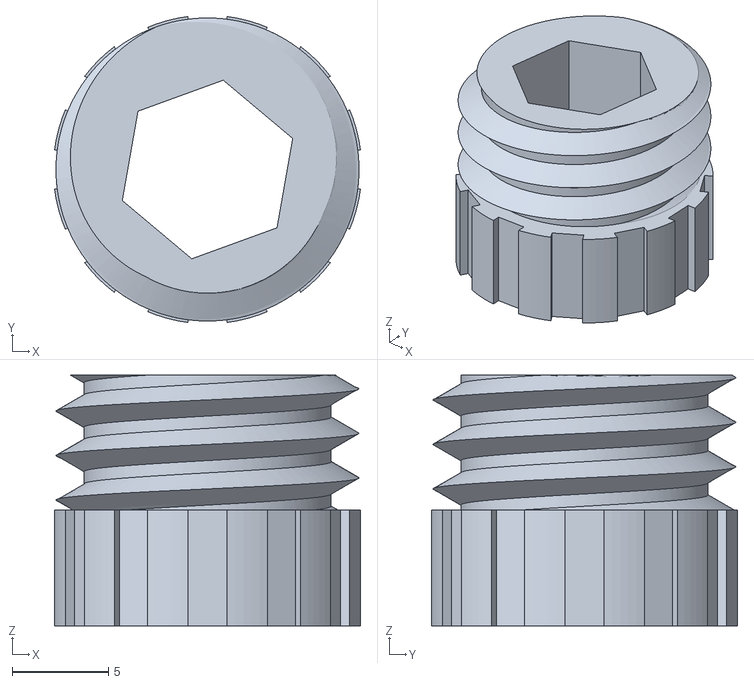
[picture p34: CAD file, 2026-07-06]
mechanical/sleeve_dipole_enclosure/cap.stl
15.9 x 15.9 x 13.0

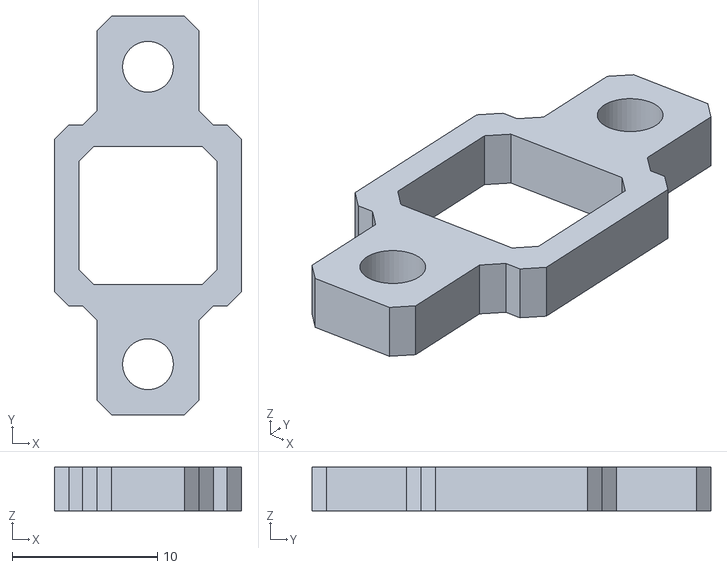
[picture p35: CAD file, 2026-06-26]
mechanical/avionics_enclosure/24clip.stl
12.9 x 27.5 x 3.00

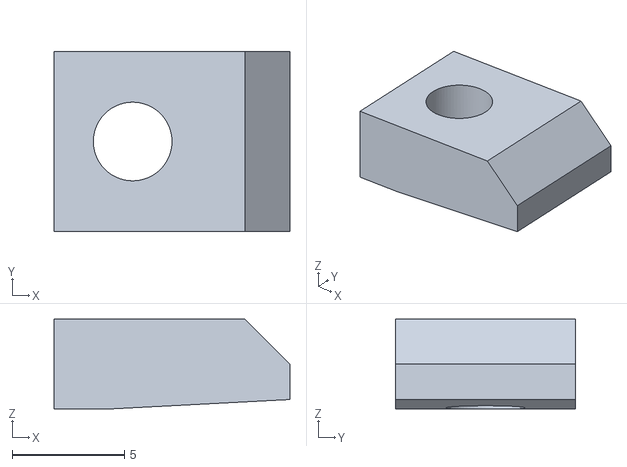
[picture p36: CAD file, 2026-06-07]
mechanical/RF_controller_enclosure/Enclosure clip.stl
10.5 x 8.00 x 4.00

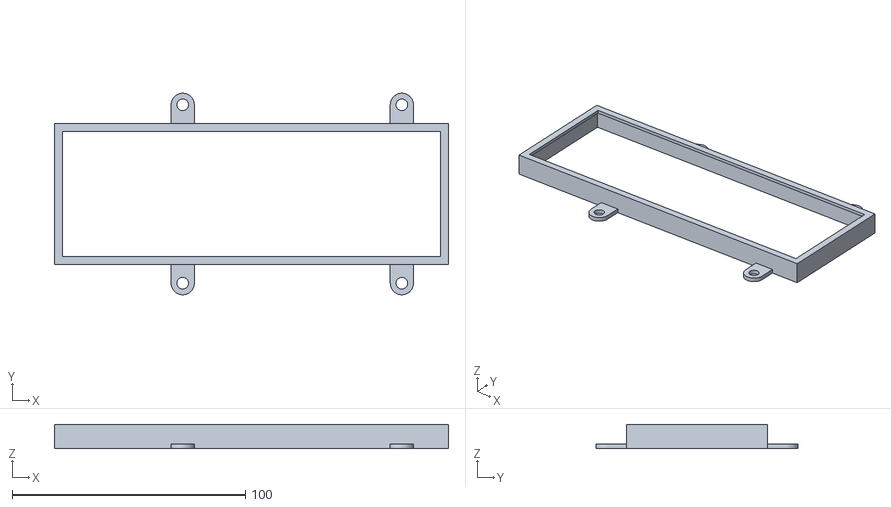
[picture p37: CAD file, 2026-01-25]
mechanical/simple_range_test/BreadboardHolder.stl
169.0 x 86.4 x 10.5

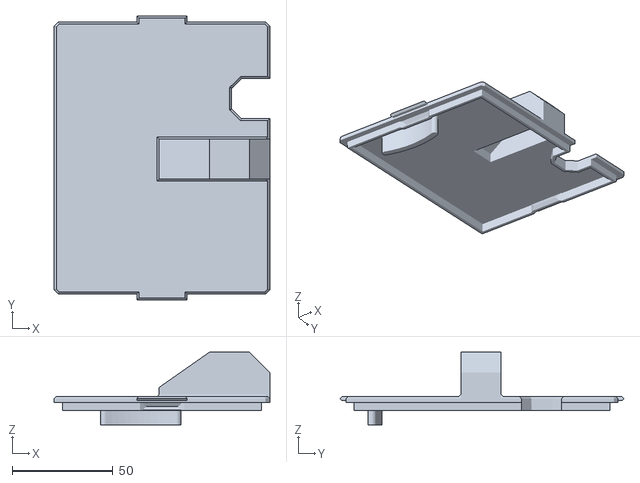
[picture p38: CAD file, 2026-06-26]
mechanical/avionics_enclosure/Lid.stl
107.0 x 141.0 x 36.0

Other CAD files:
mechanical/RF_controller_enclosure/Enclosure.3mf
mechanical/simple_range_test/EnclosureBase.stl
mechanical/avionics_enclosure/PCBClip1.stl
mechanical/avionics_enclosure/868clip.stl
mechanical/RF_controller_enclosure/24clip.stl
mechanical/RF_controller_enclosure/868clip.stl
mechanical/RF_controller_enclosure/Enclosure base.stl
mechanical/RF_controller_enclosure/Enclosure lid.stl
mechanical/avionics_enclosure/Enclosure.stl

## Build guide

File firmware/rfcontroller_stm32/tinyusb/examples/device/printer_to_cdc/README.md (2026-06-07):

#### Printer to CDC

This example demonstrates a USB composite device with a Printer class interface and a CDC serial interface. Data flows bidirectionally between the two:

- Data sent to the Printer (from host) is forwarded to the CDC serial port
- Data sent to the CDC serial port (from host) is forwarded to the Printer IN endpoint

This is useful for debugging printer class communication or as a reference for implementing printer class devices.

#### USB Interfaces

| Interface | Class | Description |
|---|---|---|
| 0 | CDC ACM | Virtual serial port |
| 2 | Printer | USB Printer (bidirectional, protocol 2) |

#### How to Test

The device exposes two endpoints on the host:
- `/dev/ttyACM0` (CDC serial port)
- `/dev/usb/lp0` (USB printer)

Note: the actual device numbers may vary depending on your system.

**Prerequisites (Linux):**

```bash
# Load the USB printer kernel module if not already loaded
sudo modprobe usblp

# Check devices exist
ls /dev/ttyACM* /dev/usb/lp*
```

**Test Printer to CDC (host writes to printer, reads from CDC):**

```bash
# Terminal 1: read from CDC
cat /dev/ttyACM0

# Terminal 2: write to printer
echo "hello from printer" > /dev/usb/lp0
# "hello from printer" appears in Terminal 1
```

**Test CDC to Printer (host writes to CDC, reads from printer):**

```bash
# Terminal 1: read from printer IN endpoint
cat /dev/usb/lp0

# Terminal 2: write to CDC
echo "hello from cdc" > /dev/ttyACM0
# "hello from cdc" appears in Terminal 1
```

**Interactive bidirectional test:**

```bash
# Terminal 1: open CDC serial port
minicom -D /dev/ttyACM0

# Terminal 2: send to printer
echo "tinyusb print example" > /dev/usb/lp0
# Text appears in minicom. Type in minicom to send data back through printer TX.
```

#### IEEE 1284 Device ID

The device responds to GET_DEVICE_ID requests with:

```
MFG:TinyUSB;MDL:Printer to CDC;CMD:PS;CLS:PRINTER;
```

Verify with:

```bash
cat /sys/class/usbmisc/lp0/device/ieee1284_id
```

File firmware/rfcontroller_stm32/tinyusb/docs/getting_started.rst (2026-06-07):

***************
Getting Started
***************

This guide will get you up and running with TinyUSB quickly with working examples.

Project Structure
====================

TinyUSB separates example applications from board-specific hardware configurations:

* **Example applications**: Located in `examples/ <https://github.com/hathach/tinyusb/tree/master/examples/>`_ directories
* **Board Support Packages (BSP)**: Located in ``hw/bsp/FAMILY/boards/BOARD_NAME/`` with hardware abstraction including pin mappings, clock settings, and linker scripts
* **Build system**: Located in `examples/build_system/ <https://github.com/hathach/tinyusb/tree/master/examples/build_system>`_ which supports both Make and CMake. Though some MCU families such as espressif or rp2040 only support cmake

For example, stm32h743eval is located in `hw/bsp/stm32h7/boards/stm32h743eval <https://github.com/hathach/tinyusb/tree/master/hw/bsp/stm32h7/boards/stm32h743eval>`_ where ``FAMILY=stm32h7`` and ``BOARD=stm32h743eval``. When you build with ``BOARD=stm32h743eval``, the build system automatically finds the corresponding BSP using the FAMILY.

For guidance on integrating TinyUSB into your own firmware (configuration, descriptors, initialization, and callback workflow), see :doc:`integration`.

Quick Start Examples
====================

The fastest way to understand TinyUSB is to see it working. These examples demonstrate core functionality and can be built immediately.

We'll assume you are using the **STM32H743 Eval board** (BOARD=stm32h743eval) under the **stm32h7** family. For other boards, see ``Board Support Packages`` below.

Get the Code
------------

.. code-block:: bash

   $ git clone https://github.com/hathach/tinyusb tinyusb
   $ cd tinyusb
   $ python tools/get_deps.py -b stm32h743eval  # or python tools/get_deps.py stm32h7

.. note::
   Some MCU families require additional SDKs, please follow their instructions to install and set it up

   * **rp2040**: Requires `pico-sdk <https://github.com/raspberrypi/pico-sdk>`_
   * **Espressif (esp32)**: Requires `esp-idf <https://github.com/espressif/esp-idf>`_. Only a few examples support the ESP-IDF build system. Look for ones with `src/CMakeLists.txt` that contain `idf_component_register()`, such as `cdc_msc_freertos`.
.. note::
   For MacOS native build with arm-none-eabi-gcc toolchain it's better to install it via brew install --cask gcc-arm-embedded

Simple Device Example
---------------------

The `cdc_msc <https://github.com/hathach/tinyusb/tree/master/examples/device/cdc_msc>`_ example creates a USB device with both a virtual serial port (CDC) and mass storage (MSC).

**What it does:**

* Appears as a serial port that echoes back any text you send
* Appears as a small USB drive with a README.TXT file
* Blinks an LED to show activity

**Build and run with CMake:**

.. code-block:: bash

   $ cd examples/device/cdc_msc
   $ cmake -DBOARD=stm32h743eval -B build # add "-G Ninja" to use Ninja build
   $ cmake --build build
   # cmake --build build --target cdc_msc-jlink

.. tip::
   Flashed/Debugger can be selected with --target ``-jlink``, ``-stlink`` or ``-openocd`` depending on your board. Use ``--target help`` to list all supported targets.

**Build and run with Make:**

.. code-block:: bash

   $ cd examples/device/cdc_msc
   $ make BOARD=stm32h743eval all
   $ make BOARD=stm32h743eval flash-jlink

.. tip::
   Flashed/Debugger can be selected with target ``flash-jlink``, ``flash-stlink`` or ``flash-openocd`` depending on your board.

Connect the device to your computer and you'll see both a new serial port and a small USB drive appear.

Simple Host Example
-------------------

The `cdc_msc_hid <https://github.com/hathach/tinyusb/tree/master/examples/host/cdc_msc_hid>`_ example creates a USB host that can connect to USB devices with CDC, MSC, or HID interfaces.

**What it does:**

* Detects and enumerates connected USB devices
* Communicates with CDC devices (like USB-to-serial adapters)
* Reads from MSC devices (like USB drives)
* Receives input from HID devices (like keyboards and mice)

**Build and run with CMake:**

.. code-block:: bash

   $ cd examples/host/cdc_msc_hid
   $ cmake -DBOARD=stm32h743eval -B build
   $ cmake --build build

**Build and run with Make:**

.. code-block:: bash

   $ cd examples/host/cdc_msc_hid
   $ make BOARD=stm32h743eval all
   $ make BOARD=stm32h743eval flash-jlink

Connect USB devices to see enumeration messages and device-specific interactions in the serial output.

Additional Build Options
------------------------

Debug and Logging
^^^^^^^^^^^^^^^^^

TinyUSB built-in logging can be enabled by setting `CFG_TUSB_DEBUG` which is done by passing ``LOG=level``. The higher the level, the more verbose the logging.

In addition to traditional hw uart as default, logging with debugger such as `Segger RTT <https://www.segger.com/products/debug-probes/j-link/technology/about-real-time-transfer/>`_ (10x faster) is also supported with `LOGGER=rtt` option.

.. code-block:: bash

   $ cmake -B build -DBOARD=stm32h743eval -DLOG=2               # logging level 2 with uart
   $ cmake -B build -DBOARD=stm32h743eval -DLOG=2 -DLOGGER=rtt  # logging level 2 with RTT

.. code-block:: bash

   $ make BOARD=stm32h743eval LOG=2 all              # logging level 2 with uart
   $ make BOARD=stm32h743eval LOG=2 LOGGER=rtt all   # logging level 2 with RTT

RootHub Port Selection
^^^^^^^^^^^^^^^^^^^^^^

Some boards support multiple usb controllers (roothub ports), by default one rh port is used as device, another as host in ``board.mk/board.cmake``. This can be overridden with option ``RHPORT_DEVICE=n`` or ``RHPORT_HOST=n`` To choose another port. For example to select the HS port of a STM32F746Disco board, use:

.. code-block:: bash

   $ cmake -B build -DBOARD=stm32h743eval -DRHPORT_DEVICE=1 # select roothub port 1 as device

.. code-block:: bash

   $ make BOARD=stm32h743eval RHPORT_DEVICE=1 all # select roothub port 1 as device

RootHub Port Speed
^^^^^^^^^^^^^^^^^^

A MCU can support multiple operational speed. By default, the example build system will use the fastest supported on the board. Use option ``RHPORT_DEVICE_SPEED=OPT_MODE_FULL/HIGH_SPEED/`` or ``RHPORT_HOST_SPEED=OPT_MODE_FULL/HIGH_SPEED/`` e.g To force operating speed

.. code-block:: bash

   $ cmake -B build -DBOARD=stm32h743eval -DRHPORT_DEVICE_SPEED=OPT_MODE_FULL_SPEED

.. code-block:: bash

   $ make BOARD=stm32h743eval RHPORT_DEVICE_SPEED=OPT_MODE_FULL_SPEED all

IAR Embedded Workbench
----------------------

For IAR users, project connection files are available. Import `tools/iar_template.ipcf <https://github.com/hathach/tinyusb/tree/master/tools/iar_template.ipcf>`_ or use native CMake support (IAR 9.50.1+). See `tools/iar_gen.py <https://github.com/hathach/tinyusb/tree/master/tools/iar_gen.py>`_ for automated project generation.

Common Issues and Solutions
---------------------------

**Build Errors**

* **"arm-none-eabi-gcc: command not found"**: Install ARM GCC toolchain: ``sudo apt-get install gcc-arm-none-eabi``
* **"Board 'X' not found"**: Check the available boards in ``hw/bsp/FAMILY/boards/`` or run ``python tools/build.py -l``
* **Missing dependencies**: Run ``python tools/get_deps.py FAMILY`` where FAMILY matches your board or ``python tools/get_deps.py -b BOARD``

**Runtime Issues**

* **Device not recognized**: Check USB descriptors implementation and ``tusb_config.h`` settings
* **Enumeration failure**: Enable logging with ``LOG=2`` and check for USB protocol errors
* **Hard faults/crashes**: Verify interrupt handler setup and stack size allocation

**Linux Permissions**

Some examples require udev permissions to access USB devices:

.. code-block:: bash

   $ cp `examples/device/99-tinyusb.rules <https://github.com/hathach/tinyusb/tree/master/examples/device/99-tinyusb.rules>`_ /etc/udev/rules.d/
   $ sudo udevadm control --reload-rules && sudo udevadm trigger

Next Steps
==========

* Check :doc:`integration` for integrating TinyUSB into your own firmware
* Check :doc:`reference/boards` for board-specific information
* Explore more examples in `examples/device/ <https://github.com/hathach/tinyusb/tree/master/examples/device>`_ and `examples/host/ <https://github.com/hathach/tinyusb/tree/master/examples/host>`_ directories
* Read :doc:`reference/usb_concepts` to understand USB fundamentals

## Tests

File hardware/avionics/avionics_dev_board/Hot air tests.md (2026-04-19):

All tests using smaller nozzle attachment.

Testing conditions to soak safely at 150C:

* Could not get temperature above 150C when heating bottom up @ 200C and 1 air flow.
* Could not get temperature above 150C when heating bottom up @ 200C and 3 air flow.
* Could not get temperature above 150C when heating bottom up @ 220C and 3 air flow.
* Temperature reached 150C when heating bottom up @ 250C and 3 air flow in \~45 seconds, max 170C in 2m30s. BMP area reached 150C briefly after \~2m heating.
* Temperature reached 150C when heating bottom up @ 235C and 3 air flow in \~55 seconds, max 164C in 2m30s.

No visible scorching after any test.

Testing conditions to ramp up temperature to 190-200C in \~15s. Area was brought to 150-155C before ramping up to the stated temperature:

* Temperature reached 170C when heating bottom up @ 300C and 3 air flow in 15 seconds, 183C in 30s. BMP area reached maximum of 158C at 30s.
* Temperature reached 185C when heating bottom up @ 320C and 3 air flow in 15 seconds, 193C in 30s. BMP area reached maximum of 163C at 30s.

No visible scorching after any test.

Testing full reflow with a dummy chip. Soak at 150C using 235C air at a flow rate of 3. Then ramp up air temperature to 320C and keep on the area for 25-30s:

Soldered well except for a few pads. Retried and kept heat on for around 60-70 seconds and the issue was resolved.

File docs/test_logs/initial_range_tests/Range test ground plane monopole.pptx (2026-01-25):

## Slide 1

SIDE PROFILE

TOP PROFILE

~90mm

Monopole

Ground plane wires

12.5 mm

45°

~100mm

SMA female panel mount

12.5 mm

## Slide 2

CONNECTION

SMA female panel mount

To NanoVNA or transceiver

SMA male

SMA female

RG316

## Notes

- Build the monopole and ground wires to be 90/100mm long initially and then trim using NanoVNA to tune
- Ground wires will be two wires with each end extending beyond the mount to make 4 radials. Total length to cut initially: 100 x 2 + 12.5 = ~215mm
- Use SMA male to male for connection

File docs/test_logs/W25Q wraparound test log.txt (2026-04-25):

**********************************************************************************************************************************************************************
FIRST TEST OF SIMPLE WRAPAROUND WITH NO BAD BLOCK
**********************************************************************************************************************************************************************

Starting W25Q wraparound management test
Erased block 0x00000000
Erased block 0x00010000
Erased block 0x00020000
Erased block 0x00030000
Erased block 0x00040000
Erased block 0x00050000
Erased block 0x00060000
Erased block 0x00070000
Erased block 0x00080000
Erased block 0x00090000
Did not find metadata, writing blank...
Erased sector 0x00000000
Writing metadata to 0x00010000
W25Q initialized - JEDEC ID verified
Current section boundaries: MS=0x00010000, ME=0x00010FFF, DS=0x00001000, DE=0x00001000
Moving empty data section to the last sector address: 0x1FFF000
Writing 25 pages (6400 bytes) of test data. Should span from 0x1FFF000 to 0x900...
Flight data written. New bounds: 0x01FFF000 to 0x01FFF063
Flight data written. New bounds: 0x01FFF000 to 0x01FFF0C7
Flight data written. New bounds: 0x01FFF000 to 0x01FFF12B
Flight data written. New bounds: 0x01FFF000 to 0x01FFF18F
Flight data written. New bounds: 0x01FFF000 to 0x01FFF1F3
Flight data written. New bounds: 0x01FFF000 to 0x01FFF257
Flight data written. New bounds: 0x01FFF000 to 0x01FFF2BB
Flight data written. New bounds: 0x01FFF000 to 0x01FFF31F
Flight data written. New bounds: 0x01FFF000 to 0x01FFF383
Flight data written. New bounds: 0x01FFF000 to 0x01FFF3E7
Flight data written. New bounds: 0x01FFF000 to 0x01FFF44B
Flight data written. New bounds: 0x01FFF000 to 0x01FFF4AF
Flight data written. New bounds: 0x01FFF000 to 0x01FFF513
Flight data written. New bounds: 0x01FFF000 to 0x01FFF577
Flight data written. New bounds: 0x01FFF000 to 0x01FFF5DB
Flight data written. New bounds: 0x01FFF000 to 0x01FFF63F
Flight data written. New bounds: 0x01FFF000 to 0x01FFF6A3
Flight data written. New bounds: 0x01FFF000 to 0x01FFF707
Flight data written. New bounds: 0x01FFF000 to 0x01FFF76B
Flight data written. New bounds: 0x01FFF000 to 0x01FFF7CF
Flight data written. New bounds: 0x01FFF000 to 0x01FFF833
Flight data written. New bounds: 0x01FFF000 to 0x01FFF897
Flight data written. New bounds: 0x01FFF000 to 0x01FFF8FB
Flight data written. New bounds: 0x01FFF000 to 0x01FFF95F
Flight data written. New bounds: 0x01FFF000 to 0x01FFF9C3
Flight data written. New bounds: 0x01FFF000 to 0x01FFFA27
Flight data written. New bounds: 0x01FFF000 to 0x01FFFA8B
Flight data written. New bounds: 0x01FFF000 to 0x01FFFAEF
Flight data written. New bounds: 0x01FFF000 to 0x01FFFB53
Flight data written. New bounds: 0x01FFF000 to 0x01FFFBB7
Flight data written. New bounds: 0x01FFF000 to 0x01FFFC1B
Flight data written. New bounds: 0x01FFF000 to 0x01FFFC7F
Flight data written. New bounds: 0x01FFF000 to 0x01FFFCE3
Flight data written. New bounds: 0x01FFF000 to 0x01FFFD47
Flight data written. New bounds: 0x01FFF000 to 0x01FFFDAB
Flight data written. New bounds: 0x01FFF000 to 0x01FFFE0F
Flight data written. New bounds: 0x01FFF000 to 0x01FFFE73
Flight data written. New bounds: 0x01FFF000 to 0x01FFFED7
Flight data written. New bounds: 0x01FFF000 to 0x01FFFF3B
Flight data written. New bounds: 0x01FFF000 to 0x01FFFF9F
WARNING: Address wraparound in W25Q_GetSafeContiguousWriteAddress
Flight data written. New bounds: 0x01FFF000 to 0x00000003
Flight data written. New bounds: 0x01FFF000 to 0x00000067
Flight data written. New bounds: 0x01FFF000 to 0x000000CB
Flight data written. New bounds: 0x01FFF000 to 0x0000012F
Flight data written. New bounds: 0x01FFF000 to 0x00000193
Flight data written. New bounds: 0x01FFF000 to 0x000001F7
Flight data written. New bounds: 0x01FFF000 to 0x0000025B
Flight data written. New bounds: 0x01FFF000 to 0x000002BF
Flight data written. New bounds: 0x01FFF000 to 0x00000323
Flight data written. New bounds: 0x01FFF000 to 0x00000387
Flight data written. New bounds: 0x01FFF000 to 0x000003EB
Flight data written. New bounds: 0x01FFF000 to 0x0000044F
Flight data written. New bounds: 0x01FFF000 to 0x000004B3
Flight data written. New bounds: 0x01FFF000 to 0x00000517
Flight data written. New bounds: 0x01FFF000 to 0x0000057B
Flight data written. New bounds: 0x01FFF000 to 0x000005DF
Flight data written. New bounds: 0x01FFF000 to 0x00000643
Flight data written. New bounds: 0x01FFF000 to 0x000006A7
Flight data written. New bounds: 0x01FFF000 to 0x0000070B
Flight data written. New bounds: 0x01FFF000 to 0x0000076F
Flight data written. New bounds: 0x01FFF000 to 0x000007D3
Flight data written. New bounds: 0x01FFF000 to 0x00000837
Flight data written. New bounds: 0x01FFF000 to 0x0000089B
Flight data written. New bounds: 0x01FFF000 to 0x000008FF
Reading back data from address 0x01FFF000...
Read volume from 0x01FFF000 to 0x01FFF0FF:
AA BB BB AA 01 00 64 00 10 5A 01 02 03 04 05 06 07 08 09 0A 0B 0C 0D 0E 0F 10 11 12 13 14 15 16 17 18 19 1A 1B 1C 1D 1E 1F 20 21 22 23 24 25 26 27 28 29 2A 2B 2C 2D 2E 2F 30 31 32 33 34 35 36 37 38 39 3A 3B 3C 3D 3E 3F 40 41 42 43 44 45 46 47 48 49 4A 4B 4C 4D 4E 4F 50 51 52 53 54 55 56 57 58 59 5A AA BB BB AA 01 00 64 00 10 5A 01 02 03 04 05 06 07 08 09 0A 0B 0C 0D 0E 0F 10 11 12 13 14 15 16 17 18 19 1A 1B 1C 1D 1E 1F 20 21 22 23 24 25 26 27 28 29 2A 2B 2C 2D 2E 2F 30 31 32 33 34 35 36 37 38 39 3A 3B 3C 3D 3E 3F 40 41 42 43 44 45 46 47 48 49 4A 4B 4C 4D 4E 4F 50 51 52 53 54 55 56 57 58 59 5A AA BB BB AA 01 00 64 00 10 5A 01 02 03 04 05 06 07 08 09 0A 0B 0C 0D 0E 0F 10 11 12 13 14 15 16 17 18 19 1A 1B 1C 1D 1E 1F 20 21 22 23 24 25 26 27 28 29 2A 2B 2C 2D 2E 
Read volume from 0x01FFF100 to 0x01FFF1FF:
2F 30 31 32 33 34 35 36 37 38 39 3A 3B 3C 3D 3E 3F 40 41 42 43 44 45 46 47 48 49 4A 4B 4C 4D 4E 4F 50 51 52 53 54 55 56 57 58 59 5A AA BB BB AA 01 00 64 00 10 5A 01 02 03 04 05 06 07 08 09 0A 0B 0C 0D 0E 0F 10 11 12 13 14 15 16 17 18 19 1A 1B 1C 1D 1E 1F 20 21 22 23 24 25 26 27 28 29 2A 2B 2C 2D 2E 2F 30 31 32 33 34 35 36 37 38 39 3A 3B 3C 3D 3E 3F 40 41 42 43 44 45 46 47 48 49 4A 4B 4C 4D 4E 4F 50 51 52 53 54 55 56 57 58 59 5A AA BB BB AA 01 00 64 00 10 5A 01 02 03 04 05 06 07 08 09 0A 0B 0C 0D 0E 0F 10 11 12 13 14 15 16 17 18 19 1A 1B 1C 1D 1E 1F 20 21 22 23 24 25 26 27 28 29 2A 2B 2C 2D 2E 2F 30 31 32 33 34 35 36 37 38 39 3A 3B 3C 3D 3E 3F 40 41 42 43 44 45 46 47 48 49 4A 4B 4C 4D 4E 4F 50 51 52 53 54 55 56 57 58 59 5A AA BB BB AA 01 00 64 00 10 5A 01 02 
Read volume from 0x01FFF200 to 0x01FFF2FF:
03 04 05 06 07 08 09 0A 0B 0C 0D 0E 0F 10 11 12 13 14 15 16 17 18 19 1A 1B 1C 1D 1E 1F 20 21 22 23 24 25 26 27 28 29 2A 2B 2C 2D 2E 2F 30 31 32 33 34 35 36 37 38 39 3A 3B 3C 3D 3E 3F 40 41 42 43 44 45 46 47 48 49 4A 4B 4C 4D 4E 4F 50 51 52 53 54 55 56 57 58 59 5A AA BB BB AA 01 00 64 00 10 5A 01 02 03 04 05 06 07 08 09 0A 0B 0C 0D 0E 0F 10 11 12 13 14 15 16 17 18 19 1A 1B 1C 1D 1E 1F 20 21 22 23 24 25 26 27 28 29 2A 2B 2C 2D 2E 2F 30 31 32 33 34 35 36 37 38 39 3A 3B 3C 3D 3E 3F 40 41 42 43 44 45 46 47 48 49 4A 4B 4C 4D 4E 4F 50 51 52 53 54 55 56 57 58 59 5A AA BB BB AA 01 00 64 00 10 5A 01 02 03 04 05 06 07 08 09 0A 0B 0C 0D 0E 0F 10 11 12 13 14 15 16 17 18 19 1A 1B 1C 1D 1E 1F 20 21 22 23 24 25 26 27 28 29 2A 2B 2C 2D 2E 2F 30 31 32 33 34 35 36 37 38 39 3A 
Read volume from 0x01FFF300 to 0x01FFF3FF:
3B 3C 3D 3E 3F 40 41 42 43 44 45 46 47 48 49 4A 4B 4C 4D 4E 4F 50 51 52 53 54 55 56 57 58 59 5A AA BB BB AA 01 00 64 00 10 5A 01 02 03 04 05 06 07 08 09 0A 0B 0C 0D 0E 0F 10 11 12 13 14 15 16 17 18 19 1A 1B 1C 1D 1E 1F 20 21 22 23 24 25 26 27 28 29 2A 2B 2C 2D 2E 2F 30 31 32 33 34 35 36 37 38 39 3A 3B 3C 3D 3E 3F 40 41 42 43 44 45 46 47 48 49 4A 4B 4C 4D 4E 4F 50 51 52 53 54 55 56 57 58 59 5A AA BB BB AA 01 00 64 00 10 5A 01 02 03 04 05 06 07 08 09 0A 0B 0C 0D 0E 0F 10 11 12 13 14 15 16 17 18 19 1A 1B 1C 1D 1E 1F 20 21 22 23 24 25 26 27 28 29 2A 2B 2C 2D 2E 2F 30 31 32 33 34 35 36 37 38 39 3A 3B 3C 3D 3E 3F 40 41 42 43 44 45 46 47 48 49 4A 4B 4C 4D 4E 4F 50 51 52 53 54 55 56 57 58 59 5A AA BB BB AA 01 00 64 00 10 5A 01 02 03 04 05 06 07 08 09 0A 0B 0C 0D 0E 
Read volume from 0x01FFF400 to 0x01FFF4FF:
0F 10 11 12 13 14 15 16 17 18 19 1A 1B 1C 1D 1E 1F 20 21 22 23 24 25 26 27 28 29 2A 2B 2C 2D 2E 2F 30 31 32 33 34 35 36 37 38 39 3A 3B 3C 3D 3E 3F 40 41 42 43 44 45 46 47 48 49 4A 4B 4C 4D 4E 4F 50 51 52 53 54 55 56 57 58 59 5A AA BB BB AA 01 00 64 00 10 5A 01 02 03 04 05 06 07 08 09 0A 0B 0C 0D 0E 0F 10 11 12 13 14 15 16 17 18 19 1A 1B 1C 1D 1E 1F 20 21 22 23 24 25 26 27 28 29 2A 2B 2C 2D 2E 2F 30 31 32 33 34 35 36 37 38 39 3A 3B 3C 3D 3E 3F 40 41 42 43 44 45 46 47 48 49 4A 4B 4C 4D 4E 4F 50 51 52 53 54 55 56 57 58 59 5A AA BB BB AA 01 00 64 00 10 5A 01 02 03 04 05 06 07 08 09 0A 0B 0C 0D 0E 0F 10 11 12 13 14 15 16 17 18 19 1A 1B 1C 1D 1E 1F 20 21 22 23 24 25 26 27 28 29 2A 2B 2C 2D 2E 2F 30 31 32 33 34 35 36 37 38 39 3A 3B 3C 3D 3E 3F 40 41 42 43 44 45 46 
Read volume from 0x01FFF500 to 0x01FFF5FF:
47 48 49 4A 4B 4C 4D 4E 4F 50 51 52 53 54 55 56 57 58 59 5A AA BB BB AA 01 00 64 00 10 5A 01 02 03 04 05 06 07 08 09 0A 0B 0C 0D 0E 0F 10 11 12 13 14 15 16 17 18 19 1A 1B 1C 1D 1E 1F 20 21 22 23 24 25 26 27 28 29 2A 2B 2C 2D 2E 2F 30 31 32 33 34 35 36 37 38 39 3A 3B 3C 3D 3E 3F 40 41 42 43 44 45 46 47 48 49 4A 4B 4C 4D 4E 4F 50 51 52 53 54 55 56 57 58 59 5A AA BB BB AA 01 00 64 00 10 5A 01 02 03 04 05 06 07 08 09 0A 0B 0C 0D 0E 0F 10 11 12 13 14 15 16 17 18 19 1A 1B 1C 1D 1E 1F 20 21 22 23 24 25 26 27 28 29 2A 2B 2C 2D 2E 2F 30 31 32 33 34 35 36 37 38 39 3A 3B 3C 3D 3E 3F 40 41 42 43 44 45 46 47 48 49 4A 4B 4C 4D 4E 4F 50 51 52 53 54 55 56 57 58 59 5A AA BB BB AA 01 00 64 00 10 5A 01 02 03 04 05 06 07 08 09 0A 0B 0C 0D 0E 0F 10 11 12 13 14 15 16 17 18 19 1A 
Read volume from 0x01FFF600 to 0x01FFF6FF:
1B 1C 1D 1E 1F 20 21 22 23 24 25 26 27 28 29 2A 2B 2C 2D 2E 2F 30 31 32 33 34 35 36 37 38 39 3A 3B 3C 3D 3E 3F 40 41 42 43 44 45 46 47 48 49 4A 4B 4C 4D 4E 4F 50 51 52 53 54 55 56 57 58 59 5A AA BB BB AA 01 00 64 00 10 5A 01 02 03 04 05 06 07 08 09 0A 0B 0C 0D 0E 0F 10 11 12 13 14 15 16 17 18 19 1A 1B 1C 1D 1E 1F 20 21 22 23 24 25 26 27 28 29 2A 2B 2C 2D 2E 2F 30 31 32 33 34 35 36 37 38 39 3A 3B 3C 3D 3E 3F 40 41 42 43 44 45 46 47 48 49 4A 4B 4C 4D 4E 4F 50 51 52 53 54 55 56 57 58 59 5A AA BB BB AA 01 00 64 00 10 5A 01 02 03 04 05 06 07 08 09 0A 0B 0C 0D 0E 0F 10 11 12 13 14 15 16 17 18 19 1A 1B 1C 1D 1E 1F 20 21 22 23 24 25 26 27 28 29 2A 2B 2C 2D 2E 2F 30 31 32 33 34 35 36 37 38 39 3A 3B 3C 3D 3E 3F 40 41 42 43 44 45 46 47 48 49 4A 4B 4C 4D 4E 4F 50 51 52 
Read volume from 0x01FFF700 to 0x01FFF7FF:
53 54 55 56 57 58 59 5A AA BB BB AA 01 00 64 00 10 5A 01 02 03 04 05 06 07 08 09 0A 0B 0C 0D 0E 0F 10 11 12 13 14 15 16 17 18 19 1A 1B 1C 1D 1E 1F 20 21 22 23 24 25 26 27 28 29 2A 2B 2C 2D 2E 2F 30 31 32 33 34 35 36 37 38 39 3A 3B 3C 3D 3E 3F 40 41 42 43 44 45 46 47 48 49 4A 4B 4C 4D 4E 4F 50 51 52 53 54 55 56 57 58 59 5A AA BB BB AA 01 00 64 00 10 5A 01 02 03 04 05 06 07 08 09 0A 0B 0C 0D 0E 0F 10 11 12 13 14 15 16 17 18 19 1A 1B 1C 1D 1E 1F 20 21 22 23 24 25 26 27 28 29 2A 2B 2C 2D 2E 2F 30 31 32 33 34 35 36 37 38 39 3A 3B 3C 3D 3E 3F 40 41 42 43 44 45 46 47 48 49 4A 4B 4C 4D 4E 4F 50 51 52 53 54 55 56 57 58 59 5A AA BB BB AA 01 00 64 00 10 5A 01 02 03 04 05 06 07 08 09 0A 0B 0C 0D 0E 0F 10 11 12 13 14 15 16 17 18 19 1A 1B 1C 1D 1E 1F 20 21 22 23 24 25 26 
Read volume from 0x01FFF800 to 0x01FFF8FF:
27 28 29 2A 2B 2C 2D 2E 2F 30 31 32 33 34 35 36 37 38 39 3A 3B 3C 3D 3E 3F 40 41 42 43 44 45 46 47 48 49 4A 4B 4C 4D 4E 4F 50 51 52 53 54 55 56 57 58 59 5A AA BB BB AA 01 00 64 00 10 5A 01 02 03 04 05 06 07 08 09 0A 0B 0C 0D 0E 0F 10 11 12 13 14 15 16 17 18 19 1A 1B 1C 1D 1E 1F 20 21 22 23 24 25 26 27 28 29 2A 2B 2C 2D 2E 2F 30 31 32 33 34 35 36 37 38 39 3A 3B 3C 3D 3E 3F 40 41 42 43 44 45 46 47 48 49 4A 4B 4C 4D 4E 4F 50 51 52 53 54 55 56 57 58 59 5A AA BB BB AA 01 00 64 00 10 5A 01 02 03 04 05 06 07 08 09 0A 0B 0C 0D 0E 0F 10 11 12 13 14 15 16 17 18 19 1A 1B 1C 1D 1E 1F 20 21 22 23 24 25 26 27 28 29 2A 2B 2C 2D 2E 2F 30 31 32 33 34 35 36 37 38 39 3A 3B 3C 3D 3E 3F 40 41 42 43 44 45 46 47 48 49 4A 4B 4C 4D 4E 4F 50 51 52 53 54 55 56 57 58 59 5A AA BB BB AA 
Read volume from 0x01FFF900 to 0x01FFF9FF:
01 00 64 00 10 5A 01 02 03 04 05 06 07 08 09 0A 0B 0C 0D 0E 0F 10 11 12 13 14 15 16 17 18 19 1A 1B 1C 1D 1E 1F 20 21 22 23 24 25 26 27 28 29 2A 2B 2C 2D 2E 2F 30 31 32 33 34 35 36 37 38 39 3A 3B 3C 3D 3E 3F 40 41 42 43 44 45 46 47 48 49 4A 4B 4C 4D 4E 4F 50 51 52 53 54 55 56 57 58 59 5A AA BB BB AA 01 00 64 00 10 5A 01 02 03 04 05 06 07 08 09 0A 0B 0C 0D 0E 0F 10 11 12 13 14 15 16 17 18 19 1A 1B 1C 1D 1E 1F 20 21 22 23 24 25 26 27 28 29 2A 2B 2C 2D 2E 2F 30 31 32 33 34 35 36 37 38 39 3A 3B 3C 3D 3E 3F 40 41 42 43 44 45 46 47 48 49 4A 4B 4C 4D 4E 4F 50 51 52 53 54 55 56 57 58 59 5A AA BB BB AA 01 00 64 00 10 5A 01 02 03 04 05 06 07 08 09 0A 0B 0C 0D 0E 0F 10 11 12 13 14 15 16 17 18 19 1A 1B 1C 1D 1E 1F 20 21 22 23 24 25 26 27 28 29 2A 2B 2C 2D 2E 2F 30 31 32 
Read volume from 0x01FFFA00 to 0x01FFFAFF:
33 34 35 36 37 38 39 3A 3B 3C 3D 3E 3F 40 41 42 43 44 45 46 47 48 49 4A 4B 4C 4D 4E 4F 50 51 52 53 54 55 56 57 58 59 5A AA BB BB AA 01 00 64 00 10 5A 01 02 03 04 05 06 07 08 09 0A 0B 0C 0D 0E 0F 10 11 12 13 14 15 16 17 18 19 1A 1B 1C 1D 1E 1F 20 21 22 23 24 25 26 27 28 29 2A 2B 2C 2D 2E 2F 30 31 32 33 34 35 36 37 38 39 3A 3B 3C 3D 3E 3F 40 41 42 43 44 45 46 47 48 49 4A 4B 4C 4D 4E 4F 50 51 52 53 54 55 56 57 58 59 5A AA BB BB AA 01 00 64 00 10 5A 01 02 03 04 05 06 07 08 09 0A 0B 0C 0D 0E 0F 10 11 12 13 14 15 16 17 18 19 1A 1B 1C 1D 1E 1F 20 21 22 23 24 25 26 27 28 29 2A 2B 2C 2D 2E 2F 30 31 32 33 34 35 36 37 38 39 3A 3B 3C 3D 3E 3F 40 41 42 43 44 45 46 47 48 49 4A 4B 4C 4D 4E 4F 50 51 52 53 54 55 56 57 58 59 5A AA BB BB AA 01 00 64 00 10 5A 01 02 03 04 05 06 
Read volume from 0x01FFFB00 to 0x01FFFBFF:
07 08 09 0A 0B 0C 0D 0E 0F 10 11 12 13 14 15 16 17 18 19 1A 1B 1C 1D 1E 1F 20 21 22 23 24 25 26 27 28 29 2A 2B 2C 2D 2E 2F 30 31 32 33 34 35 36 37 38 39 3A 3B 3C 3D 3E 3F 40 41 42 43 44 45 46 47 48 49 4A 4B 4C 4D 4E 4F 50 51 52 53 54 55 56 57 58 59 5A AA BB BB AA 01 00 64 00 10 5A 01 02 03 04 05 06 07 08 09 0A 0B 0C 0D 0E 0F 10 11 12 13 14 15 16 17 18 19 1A 1B 1C 1D 1E 1F 20 21 22 23 24 25 26 27 28 29 2A 2B 2C 2D 2E 2F 30 31 32 33 34 35 36 37 38 39 3A 3B 3C 3D 3E 3F 40 41 42 43 44 45 46 47 48 49 4A 4B 4C 4D 4E 4F 50 51 52 53 54 55 56 57 58 59 5A AA BB BB AA 01 00 64 00 10 5A 01 02 03 04 05 06 07 08 09 0A 0B 0C 0D 0E 0F 10 11 12 13 14 15 16 17 18 19 1A 1B 1C 1D 1E 1F 20 21 22 23 24 25 26 27 28 29 2A 2B 2C 2D 2E 2F 30 31 32 33 34 35 36 37 38 39 3A 3B 3C 3D 3E 
Read volume from 0x01FFFC00 to 0x01FFFCFF:
3F 40 41 42 43 44 45 46 47 48 49 4A 4B 4C 4D 4E 4F 50 51 52 53 54 55 56 57 58 59 5A AA BB BB AA 01 00 64 00 10 5A 01 02 03 04 05 06 07 08 09 0A 0B 0C 0D 0E 0F 10 11 12 13 14 15 16 17 18 19 1A 1B 1C 1D 1E 1F 20 21 22 23 24 25 26 27 28 29 2A 2B 2C 2D 2E 2F 30 31 32 33 34 35 36 37 38 39 3A 3B 3C 3D 3E 3F 40 41 42 43 44 45 46 47 48 49 4A 4B 4C 4D 4E 4F 50 51 52 53 54 55 56 57 58 59 5A AA BB BB AA 01 00 64 00 10 5A 01 02 03 04 05 06 07 08 09 0A 0B 0C 0D 0E 0F 10 11 12 13 14 15 16 17 18 19 1A 1B 1C 1D 1E 1F 20 21 22 23 24 25 26 27 28 29 2A 2B 2C 2D 2E 2F 30 31 32 33 34 35 36 37 38 39 3A 3B 3C 3D 3E 3F 40 41 42 43 44 45 46 47 48 49 4A 4B 4C 4D 4E 4F 50 51 52 53 54 55 56 57 58 59 5A AA BB BB AA 01 00 64 00 10 5A 01 02 03 04 05 06 07 08 09 0A 0B 0C 0D 0E 0F 10 11 12 
Read volume from 0x01FFFD00 to 0x01FFFDFF:
13 14 15 16 17 18 19 1A 1B 1C 1D 1E 1F 20 21 22 23 24 25 26 27 28 29 2A 2B 2C 2D 2E 2F 30 31 32 33 34 35 36 37 38 39 3A 3B 3C 3D 3E 3F 40 41 42 43 44 45 46 47 48 49 4A 4B 4C 4D 4E 4F 50 51 52 53 54 55 56 57 58 59 5A AA BB BB AA 01 00 64 00 10 5A 01 02 03 04 05 06 07 08 09 0A 0B 0C 0D 0E 0F 10 11 12 13 14 15 16 17 18 19 1A 1B 1C 1D 1E 1F 20 21 22 23 24 25 26 27 28 29 2A 2B 2C 2D 2E 2F 30 31 32 33 34 35 36 37 38 39 3A 3B 3C 3D 3E 3F 40 41 42 43 44 45 46 47 48 49 4A 4B 4C 4D 4E 4F 50 51 52 53 54 55 56 57 58 59 5A AA BB BB AA 01 00 64 00 10 5A 01 02 03 04 05 06 07 08 09 0A 0B 0C 0D 0E 0F 10 11 12 13 14 15 16 17 18 19 1A 1B 1C 1D 1E 1F 20 21 22 23 24 25 26 27 28 29 2A 2B 2C 2D 2E 2F 30 31 32 33 34 35 36 37 38 39 3A 3B 3C 3D 3E 3F 40 41 42 43 44 45 46 47 48 49 4A 
Read volume from 0x01FFFE00 to 0x01FFFEFF:
4B 4C 4D 4E 4F 50 51 52 53 54 55 56 57 58 59 5A AA BB BB AA 01 00 64 00 10 5A 01 02 03 04 05 06 07 08 09 0A 0B 0C 0D 0E 0F 10 11 12 13 14 15 16 17 18 19 1A 1B 1C 1D 1E 1F 20 21 22 23 24 25 26 27 28 29 2A 2B 2C 2D 2E 2F 30 31 32 33 34 35 36 37 38 39 3A 3B 3C 3D 3E 3F 40 41 42 43 44 45 46 47 48 49 4A 4B 4C 4D 4E 4F 50 51 52 53 54 55 56 57 58 59 5A AA BB BB AA 01 00 64 00 10 5A 01 02 03 04 05 06 07 08 09 0A 0B 0C 0D 0E 0F 10 11 12 13 14 15 16 17 18 19 1A 1B 1C 1D 1E 1F 20 21 22 23 24 25 26 27 28 29 2A 2B 2C 2D 2E 2F 30 31 32 33 34 35 36 37 38 39 3A 3B 3C 3D 3E 3F 40 41 42 43 44 45 46 47 48 49 4A 4B 4C 4D 4E 4F 50 51 52 53 54 55 56 57 58 59 5A AA BB BB AA 01 00 64 00 10 5A 01 02 03 04 05 06 07 08 09 0A 0B 0C 0D 0E 0F 10 11 12 13 14 15 16 17 18 19 1A 1B 1C 1D 1E 
Read volume from 0x01FFFF00 to 0x01FFFFFF:
1F 20 21 22 23 24 25 26 27 28 29 2A 2B 2C 2D 2E 2F 30 31 32 33 34 35 36 37 38 39 3A 3B 3C 3D 3E 3F 40 41 42 43 44 45 46 47 48 49 4A 4B 4C 4D 4E 4F 50 51 52 53 54 55 56 57 58 59 5A AA BB BB AA 01 00 64 00 10 5A 01 02 03 04 05 06 07 08 09 0A 0B 0C 0D 0E 0F 10 11 12 13 14 15 16 17 18 19 1A 1B 1C 1D 1E 1F 20 21 22 23 24 25 26 27 28 29 2A 2B 2C 2D 2E 2F 30 31 32 33 34 35 36 37 38 39 3A 3B 3C 3D 3E 3F 40 41 42 43 44 45 46 47 48 49 4A 4B 4C 4D 4E 4F 50 51 52 53 54 55 56 57 58 59 5A AA BB BB AA 01 00 64 00 10 5A 01 02 03 04 05 06 07 08 09 0A 0B 0C 0D 0E 0F 10 11 12 13 14 15 16 17 18 19 1A 1B 1C 1D 1E 1F 20 21 22 23 24 25 26 27 28 29 2A 2B 2C 2D 2E 2F 30 31 32 33 34 35 36 37 38 39 3A 3B 3C 3D 3E 3F 40 41 42 43 44 45 46 47 48 49 4A 4B 4C 4D 4E 4F 50 51 52 53 54 55 56 
WARNING: Address wraparound in W25Q_GetSafeContiguousReadAddress
Read volume from 0x00000000 to 0x000000FF:
57 58 59 5A AA BB BB AA 01 00 64 00 10 5A 01 02 03 04 05 06 07 08 09 0A 0B 0C 0D 0E 0F 10 11 12 13 14 15 16 17 18 19 1A 1B 1C 1D 1E 1F 20 21 22 23 24 25 26 27 28 29 2A 2B 2C 2D 2E 2F 30 31 32 33 34 35 36 37 38 39 3A 3B 3C 3D 3E 3F 40 41 42 43 44 45 46 47 48 49 4A 4B 4C 4D 4E 4F 50 51 52 53 54 55 56 57 58 59 5A AA BB BB AA 01 00 64 00 10 5A 01 02 03 04 05 06 07 08 09 0A 0B 0C 0D 0E 0F 10 11 12 13 14 15 16 17 18 19 1A 1B 1C 1D 1E 1F 20 21 22 23 24 25 26 27 28 29 2A 2B 2C 2D 2E 2F 30 31 32 33 34 35 36 37 38 39 3A 3B 3C 3D 3E 3F 40 41 42 43 44 45 46 47 48 49 4A 4B 4C 4D 4E 4F 50 51 52 53 54 55 56 57 58 59 5A AA BB BB AA 01 00 64 00 10 5A 01 02 03 04 05 06 07 08 09 0A 0B 0C 0D 0E 0F 10 11 12 13 14 15 16 17 18 19 1A 1B 1C 1D 1E 1F 20 21 22 23 24 25 26 27 28 29 2A 
Read volume from 0x00000100 to 0x000001FF:
2B 2C 2D 2E 2F 30 31 32 33 34 35 36 37 38 39 3A 3B 3C 3D 3E 3F 40 41 42 43 44 45 46 47 48 49 4A 4B 4C 4D 4E 4F 50 51 52 53 54 55 56 57 58 59 5A AA BB BB AA 01 00 64 00 10 5A 01 02 03 04 05 06 07 08 09 0A 0B 0C 0D 0E 0F 10 11 12 13 14 15 16 17 18 19 1A 1B 1C 1D 1E 1F 20 21 22 23 24 25 26 27 28 29 2A 2B 2C 2D 2E 2F 30 31 32 33 34 35 36 37 38 39 3A 3B 3C 3D 3E 3F 40 41 42 43 44 45 46 47 48 49 4A 4B 4C 4D 4E 4F 50 51 52 53 54 55 56 57 58 59 5A AA BB BB AA 01 00 64 00 10 5A 01 02 03 04 05 06 07 08 09 0A 0B 0C 0D 0E 0F 10 11 12 13 14 15 16 17 18 19 1A 1B 1C 1D 1E 1F 20 21 22 23 24 25 26 27 28 29 2A 2B 2C 2D 2E 2F 30 31 32 33 34 35 36 37 38 39 3A 3B 3C 3D 3E 3F 40 41 42 43 44 45 46 47 48 49 4A 4B 4C 4D 4E 4F 50 51 52 53 54 55 56 57 58 59 5A AA BB BB AA 01 00 64 00 
Read volume from 0x00000200 to 0x000002FF:
10 5A 01 02 03 04 05 06 07 08 09 0A 0B 0C 0D 0E 0F 10 11 12 13 14 15 16 17 18 19 1A 1B 1C 1D 1E 1F 20 21 22 23 24 25 26 27 28 29 2A 2B 2C 2D 2E 2F 30 31 32 33 34 35 36 37 38 39 3A 3B 3C 3D 3E 3F 40 41 42 43 44 45 46 47 48 49 4A 4B 4C 4D 4E 4F 50 51 52 53 54 55 56 57 58 59 5A AA BB BB AA 01 00 64 00 10 5A 01 02 03 04 05 06 07 08 09 0A 0B 0C 0D 0E 0F 10 11 12 13 14 15 16 17 18 19 1A 1B 1C 1D 1E 1F 20 21 22 23 24 25 26 27 28 29 2A 2B 2C 2D 2E 2F 30 31 32 33 34 35 36 37 38 39 3A 3B 3C 3D 3E 3F 40 41 42 43 44 45 46 47 48 49 4A 4B 4C 4D 4E 4F 50 51 52 53 54 55 56 57 58 59 5A AA BB BB AA 01 00 64 00 10 5A 01 02 03 04 05 06 07 08 09 0A 0B 0C 0D 0E 0F 10 11 12 13 14 15 16 17 18 19 1A 1B 1C 1D 1E 1F 20 21 22 23 24 25 26 27 28 29 2A 2B 2C 2D 2E 2F 30 31 32 33 34 35 36 
Read volume from 0x00000300 to 0x000003FF:
37 38 39 3A 3B 3C 3D 3E 3F 40 41 42 43 44 45 46 47 48 49 4A 4B 4C 4D 4E 4F 50 51 52 53 54 55 56 57 58 59 5A AA BB BB AA 01 00 64 00 10 5A 01 02 03 04 05 06 07 08 09 0A 0B 0C 0D 0E 0F 10 11 12 13 14 15 16 17 18 19 1A 1B 1C 1D 1E 1F 20 21 22 23 24 25 26 27 28 29 2A 2B 2C 2D 2E 2F 30 31 32 33 34 35 36 37 38 39 3A 3B 3C 3D 3E 3F 40 41 42 43 44 45 46 47 48 49 4A 4B 4C 4D 4E 4F 50 51 52 53 54 55 56 57 58 59 5A AA BB BB AA 01 00 64 00 10 5A 01 02 03 04 05 06 07 08 09 0A 0B 0C 0D 0E 0F 10 11 12 13 14 15 16 17 18 19 1A 1B 1C 1D 1E 1F 20 21 22 23 24 25 26 27 28 29 2A 2B 2C 2D 2E 2F 30 31 32 33 34 35 36 37 38 39 3A 3B 3C 3D 3E 3F 40 41 42 43 44 45 46 47 48 49 4A 4B 4C 4D 4E 4F 50 51 52 53 54 55 56 57 58 59 5A AA BB BB AA 01 00 64 00 10 5A 01 02 03 04 05 06 07 08 09 0A 
Read volume from 0x00000400 to 0x000004FF:
0B 0C 0D 0E 0F 10 11 12 13 14 15 16 17 18 19 1A 1B 1C 1D 1E 1F 20 21 22 23 24 25 26 27 28 29 2A 2B 2C 2D 2E 2F 30 31 32 33 34 35 36 37 38 39 3A 3B 3C 3D 3E 3F 40 41 42 43 44 45 46 47 48 49 4A 4B 4C 4D 4E 4F 50 51 52 53 54 55 56 57 58 59 5A AA BB BB AA 01 00 64 00 10 5A 01 02 03 04 05 06 07 08 09 0A 0B 0C 0D 0E 0F 10 11 12 13 14 15 16 17 18 19 1A 1B 1C 1D 1E 1F 20 21 22 23 24 25 26 27 28 29 2A 2B 2C 2D 2E 2F 30 31 32 33 34 35 36 37 38 39 3A 3B 3C 3D 3E 3F 40 41 42 43 44 45 46 47 48 49 4A 4B 4C 4D 4E 4F 50 51 52 53 54 55 56 57 58 59 5A AA BB BB AA 01 00 64 00 10 5A 01 02 03 04 05 06 07 08 09 0A 0B 0C 0D 0E 0F 10 11 12 13 14 15 16 17 18 19 1A 1B 1C 1D 1E 1F 20 21 22 23 24 25 26 27 28 29 2A 2B 2C 2D 2E 2F 30 31 32 33 34 35 36 37 38 39 3A 3B 3C 3D 3E 3F 40 41 42 
Read volume from 0x00000500 to 0x000005FF:
43 44 45 46 47 48 49 4A 4B 4C 4D 4E 4F 50 51 52 53 54 55 56 57 58 59 5A AA BB BB AA 01 00 64 00 10 5A 01 02 03 04 05 06 07 08 09 0A 0B 0C 0D 0E 0F 10 11 12 13 14 15 16 17 18 19 1A 1B 1C 1D 1E 1F 20 21 22 23 24 25 26 27 28 29 2A 2B 2C 2D 2E 2F 30 31 32 33 34 35 36 37 38 39 3A 3B 3C 3D 3E 3F 40 41 42 43 44 45 46 47 48 49 4A 4B 4C 4D 4E 4F 50 51 52 53 54 55 56 57 58 59 5A AA BB BB AA 01 00 64 00 10 5A 01 02 03 04 05 06 07 08 09 0A 0B 0C 0D 0E 0F 10 11 12 13 14 15 16 17 18 19 1A 1B 1C 1D 1E 1F 20 21 22 23 24 25 26 27 28 29 2A 2B 2C 2D 2E 2F 30 31 32 33 34 35 36 37 38 39 3A 3B 3C 3D 3E 3F 40 41 42 43 44 45 46 47 48 49 4A 4B 4C 4D 4E 4F 50 51 52 53 54 55 56 57 58 59 5A AA BB BB AA 01 00 64 00 10 5A 01 02 03 04 05 06 07 08 09 0A 0B 0C 0D 0E 0F 10 11 12 13 14 15 16 
Read volume from 0x00000600 to 0x000006FF:
17 18 19 1A 1B 1C 1D 1E 1F 20 21 22 23 24 25 26 27 28 29 2A 2B 2C 2D 2E 2F 30 31 32 33 34 35 36 37 38 39 3A 3B 3C 3D 3E 3F 40 41 42 43 44 45 46 47 48 49 4A 4B 4C 4D 4E 4F 50 51 52 53 54 55 56 57 58 59 5A AA BB BB AA 01 00 64 00 10 5A 01 02 03 04 05 06 07 08 09 0A 0B 0C 0D 0E 0F 10 11 12 13 14 15 16 17 18 19 1A 1B 1C 1D 1E 1F 20 21 22 23 24 25 26 27 28 29 2A 2B 2C 2D 2E 2F 30 31 32 33 34 35 36 37 38 39 3A 3B 3C 3D 3E 3F 40 41 42 43 44 45 46 47 48 49 4A 4B 4C 4D 4E 4F 50 51 52 53 54 55 56 57 58 59 5A AA BB BB AA 01 00 64 00 10 5A 01 02 03 04 05 06 07 08 09 0A 0B 0C 0D 0E 0F 10 11 12 13 14 15 16 17 18 19 1A 1B 1C 1D 1E 1F 20 21 22 23 24 25 26 27 28 29 2A 2B 2C 2D 2E 2F 30 31 32 33 34 35 36 37 38 39 3A 3B 3C 3D 3E 3F 40 41 42 43 44 45 46 47 48 49 4A 4B 4C 4D 4E 
Read volume from 0x00000700 to 0x000007FF:
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

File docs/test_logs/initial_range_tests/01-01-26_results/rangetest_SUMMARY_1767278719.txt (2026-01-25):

[14:45:20.759] Resetting module...
[14:45:21.265] Setting initial params...
[14:45:21.265] Listening for packets...
[14:45:21.281] Aggregated stats will output every 50 packets
[14:45:21.281] RSSI(Avg) | RSSI(Min/Max/Rng) | SNR(Avg) | Miss | CRC | PPS  | Reliability
[14:45:21.297] -----------------------------------------------------------------------
[14:45:42.932] -30.1 dBm  | -53/-25/28       | 12.6 dB |  0   |  0  | 2.3  | 100.0%
[14:45:47.055] -26.5 dBm  | -31/-22/9       | 12.7 dB |  0   |  0  | 12.1  | 100.0%
[14:45:51.185] -29.2 dBm  | -52/-20/32       | 12.7 dB |  0   |  0  | 12.1  | 100.0%
[14:45:55.316] -33.0 dBm  | -39/-26/13       | 12.6 dB |  0   |  0  | 12.1  | 100.0%
[14:45:59.457] -41.3 dBm  | -50/-36/14       | 12.6 dB |  0   |  0  | 12.1  | 100.0%
[14:46:05.532] -59.1 dBm  | -85/-47/38       | 12.6 dB |  65253   |  0  | 8.2  | 0.1%
[14:46:11.597] -56.7 dBm  | -60/-53/7       | 12.7 dB |  65519   |  0  | 8.2  | 151.5%
[14:46:15.740] -62.5 dBm  | -69/-58/11       | 12.7 dB |  0   |  0  | 12.1  | 100.0%
[14:46:21.813] -64.5 dBm  | -68/-61/7       | 12.7 dB |  65409   |  0  | 8.2  | 0.1%
[14:46:33.730] -68.8 dBm  | -71/-65/6       | 12.6 dB |  65464   |  0  | 4.2  | 0.1%
[14:46:45.651] -74.1 dBm  | -79/-69/10       | 12.5 dB |  65488   |  0  | 4.2  | 2500.0%
[14:47:01.430] -79.6 dBm  | -86/-77/9       | 12.3 dB |  65487   |  0  | 3.2  | 5000.0%
[14:47:13.314] -82.9 dBm  | -88/-80/8       | 12.2 dB |  65487   |  0  | 4.2  | 5000.0%
[14:47:32.988] -86.0 dBm  | -94/-83/11       | 11.8 dB |  65484   |  0  | 2.5  | 0.1%
[14:47:56.529] -90.3 dBm  | -96/-88/8       | 10.9 dB |  65490   |  0  | 2.1  | 1250.0%
[14:48:16.149] -93.5 dBm  | -99/-89/10       | 9.7 dB |  65482   |  0  | 2.6  | 0.1%
[14:48:39.639] -99.3 dBm  | -105/-94/11       | 5.9 dB |  65488   |  0  | 2.1  | 2500.0%
[14:49:03.190] -100.0 dBm  | -106/-90/16       | 4.7 dB |  65484   |  0  | 2.1  | 0.1%
[14:49:18.988] -91.9 dBm  | -97/-85/12       | 10.1 dB |  65488   |  0  | 3.2  | 2500.0%
[14:49:34.748] -96.5 dBm  | -101/-93/8       | 7.5 dB |  65487   |  0  | 3.2  | 5000.0%
[14:50:02.188] -95.4 dBm  | -103/-90/13       | 8.3 dB |  65481   |  0  | 1.8  | 0.1%
[14:50:29.597] -96.7 dBm  | -104/-93/11       | 8.0 dB |  65487   |  0  | 1.8  | 5000.0%
[14:51:00.941] -96.6 dBm  | -102/-92/10       | 8.5 dB |  65486   |  0  | 1.6  | inf%
[14:51:35.957] -97.3 dBm  | -105/-80/25       | 8.2 dB |  65485   |  0  | 1.4  | 0.1%
[14:51:59.355] -79.9 dBm  | -84/-75/9       | 12.7 dB |  65526   |  0  | 2.1  | 125.0%
[14:52:03.487] -80.0 dBm  | -81/-79/2       | 12.7 dB |  0   |  0  | 12.1  | 100.0%
[14:52:07.613] -82.3 dBm  | -84/-81/3       | 12.5 dB |  0   |  0  | 12.1  | 100.0%
[14:52:11.752] -81.1 dBm  | -82/-80/2       | 12.4 dB |  0   |  0  | 12.1  | 100.0%
[14:52:15.877] -84.5 dBm  | -89/-81/8       | 12.3 dB |  0   |  0  | 12.1  | 100.0%
[14:52:21.972] -88.2 dBm  | -94/-84/10       | 11.8 dB |  65266   |  0  | 8.2  | 0.1%
[14:52:26.095] -88.3 dBm  | -90/-86/4       | 12.0 dB |  0   |  0  | 12.1  | 100.0%
[14:52:30.233] -88.8 dBm  | -92/-87/5       | 12.0 dB |  0   |  0  | 12.1  | 100.0%
[14:52:34.365] -88.5 dBm  | -93/-86/7       | 11.8 dB |  0   |  0  | 12.1  | 100.0%
[14:52:40.418] -89.0 dBm  | -96/-87/9       | 11.6 dB |  65364   |  0  | 8.3  | 0.1%
[14:52:46.476] -88.4 dBm  | -93/-86/7       | 11.5 dB |  65451   |  0  | 8.2  | 0.1%
[14:52:50.604] -88.3 dBm  | -92/-86/6       | 11.7 dB |  0   |  0  | 12.1  | 100.0%
[14:52:54.738] -89.9 dBm  | -92/-88/4       | 11.0 dB |  0   |  0  | 12.1  | 100.0%
[14:53:00.819] -89.9 dBm  | -94/-86/8       | 11.2 dB |  65397   |  0  | 8.2  | 0.1%
[14:53:06.894] -91.6 dBm  | -95/-90/5       | 10.7 dB |  65486   |  0  | 8.2  | inf%
[14:53:14.929] -90.7 dBm  | -94/-88/6       | 11.1 dB |  65473   |  0  | 6.2  | 0.1%
[14:53:22.943] -92.2 dBm  | -98/-89/9       | 10.6 dB |  65492   |  0  | 6.2  | 833.3%
[14:53:32.928] -95.7 dBm  | -98/-93/5       | 9.0 dB |  65474   |  0  | 5.0  | 0.1%
[14:53:42.888] -96.2 dBm  | -100/-93/7       | 8.7 dB |  65485   |  0  | 5.0  | 0.1%
[14:53:52.860] -96.3 dBm  | -98/-94/4       | 8.6 dB |  65486   |  0  | 5.0  | inf%
[14:54:02.832] -94.0 dBm  | -98/-92/6       | 10.1 dB |  65489   |  0  | 5.0  | 1666.7%
[14:54:12.801] -97.5 dBm  | -100/-94/6       | 7.9 dB |  65488   |  0  | 5.0  | 2500.0%
[14:54:22.766] -97.4 dBm  | -101/-95/6       | 8.2 dB |  65489   |  0  | 5.0  | 1666.7%
[14:54:32.737] -98.6 dBm  | -101/-95/6       | 7.4 dB |  65488   |  0  | 5.0  | 2500.0%
[14:54:44.665] -99.4 dBm  | -104/-96/8       | 6.8 dB |  65476   |  0  | 4.2  | 0.1%
[14:54:58.593] -100.3 dBm  | -108/-92/16       | 3.4 dB |  65487   |  0  | 3.6  | 5000.0%
[14:55:20.233] -101.1 dBm  | -108/-93/15       | 4.0 dB |  65484   |  0  | 2.3  | 0.1%
[14:55:40.501] -105.2 dBm  | -109/-98/11       | -2.3 dB |  65485   |  0  | 2.5  | 0.1%
[14:55:52.407] -105.1 dBm  | -107/-103/4       | 0.7 dB |  65494   |  0  | 4.2  | 625.0%
[14:56:08.221] -103.8 dBm  | -107/-100/7       | 2.6 dB |  65477   |  0  | 3.2  | 0.1%
[14:56:22.155] -105.2 dBm  | -109/-103/6       | 0.8 dB |  65487   |  0  | 3.6  | 5000.0%
[14:56:40.808] -106.4 dBm  | -109/-103/6       | -3.5 dB |  65484   |  0  | 2.7  | 0.1%
[14:57:01.549] -106.1 dBm  | -109/-104/5       | -5.9 dB |  65490   |  0  | 2.4  | 1250.0%
[14:57:27.438] -106.9 dBm  | -109/-105/4       | -5.5 dB |  65484   |  0  | 1.9  | 0.1%
[14:58:08.296] -107.5 dBm  | -109/-106/3       | -7.2 dB |  65484   |  0  | 1.2  | 0.1%
[14:58:45.955] -105.8 dBm  | -109/-100/9       | -1.8 dB |  65489   |  0  | 1.3  | 1666.7%
[14:59:37.098] -103.1 dBm  | -109/-91/18       | 1.6 dB |  65484   |  0  | 1.0  | 0.1%
[15:00:12.275] -99.8 dBm  | -104/-96/8       | 6.0 dB |  65487   |  0  | 1.4  | 5000.0%

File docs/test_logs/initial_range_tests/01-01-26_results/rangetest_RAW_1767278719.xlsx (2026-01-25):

PC_Timestamp | Sequence | RSSI | SNR | Status
14:45:39 | 0 | -53 | 12.5 | OK
14:45:39 | 1 | -46 | 12.25 | OK
14:45:39 | 2 | -46 | 11.75 | OK
14:45:39 | 3 | -44 | 12.25 | OK
14:45:39 | 4 | -41 | 12.5 | OK
14:45:39 | 5 | -36 | 12.5 | OK
14:45:39 | 6 | -34 | 13.25 | OK
14:45:39 | 7 | -33 | 12.75 | OK
14:45:40 | 8 | -33 | 12.25 | OK
14:45:40 | 9 | -33 | 12 | OK
14:45:40 | 10 | -32 | 12.25 | OK
14:45:40 | 11 | -30 | 12.25 | OK
14:45:40 | 12 | -29 | 12.5 | OK
14:45:40 | 13 | -28 | 12.25 | OK
14:45:40 | 14 | -29 | 12.75 | OK
14:45:40 | 15 | -30 | 12.25 | OK
14:45:40 | 16 | -29 | 12 | OK
14:45:40 | 17 | -29 | 12.75 | OK
14:45:40 | 18 | -29 | 13 | OK
14:45:40 | 19 | -30 | 12.25 | OK
14:45:41 | 20 | -29 | 12.25 | OK
14:45:41 | 21 | -27 | 12.5 | OK
14:45:41 | 22 | -26 | 12.5 | OK
14:45:41 | 23 | -26 | 12.75 | OK
14:45:41 | 24 | -26 | 13.5 | OK
14:45:41 | 25 | -26 | 12.5 | OK
14:45:41 | 26 | -28 | 13 | OK
14:45:41 | 27 | -28 | 13.5 | OK
14:45:41 | 28 | -27 | 12.5 | OK
14:45:41 | 29 | -26 | 12.25 | OK
14:45:41 | 30 | -25 | 12.75 | OK
14:45:41 | 31 | -25 | 13 | OK
14:45:42 | 32 | -25 | 13.5 | OK
14:45:42 | 33 | -27 | 12.25 | OK
14:45:42 | 34 | -28 | 13.25 | OK
14:45:42 | 35 | -27 | 12.75 | OK
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

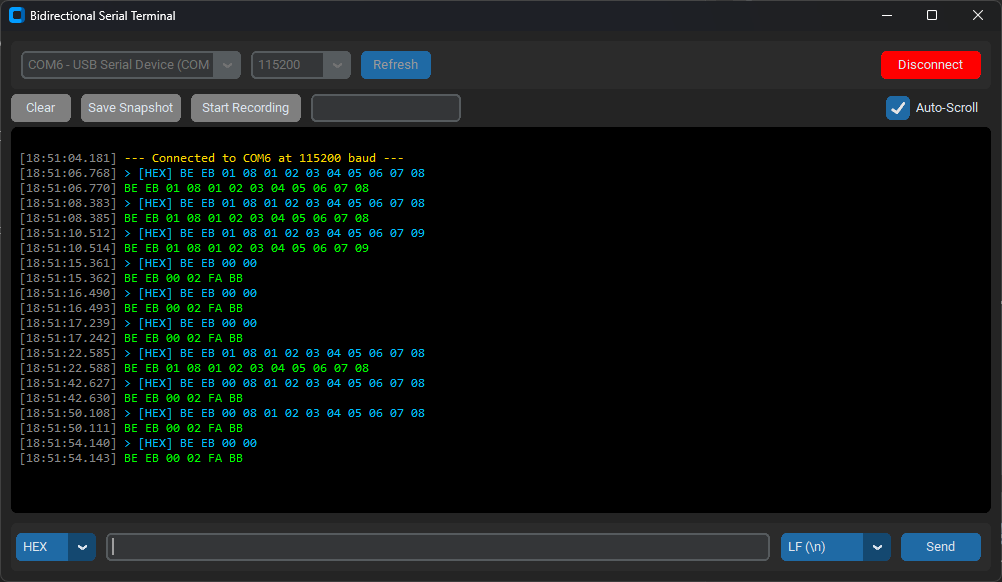
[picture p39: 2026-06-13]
docs/test_logs/RFcontroller_echo_status_output.png

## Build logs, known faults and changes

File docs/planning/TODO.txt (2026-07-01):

- Protect against INT skipping by using timers to periodically check status registers. Reset the timer every time the INT happens.

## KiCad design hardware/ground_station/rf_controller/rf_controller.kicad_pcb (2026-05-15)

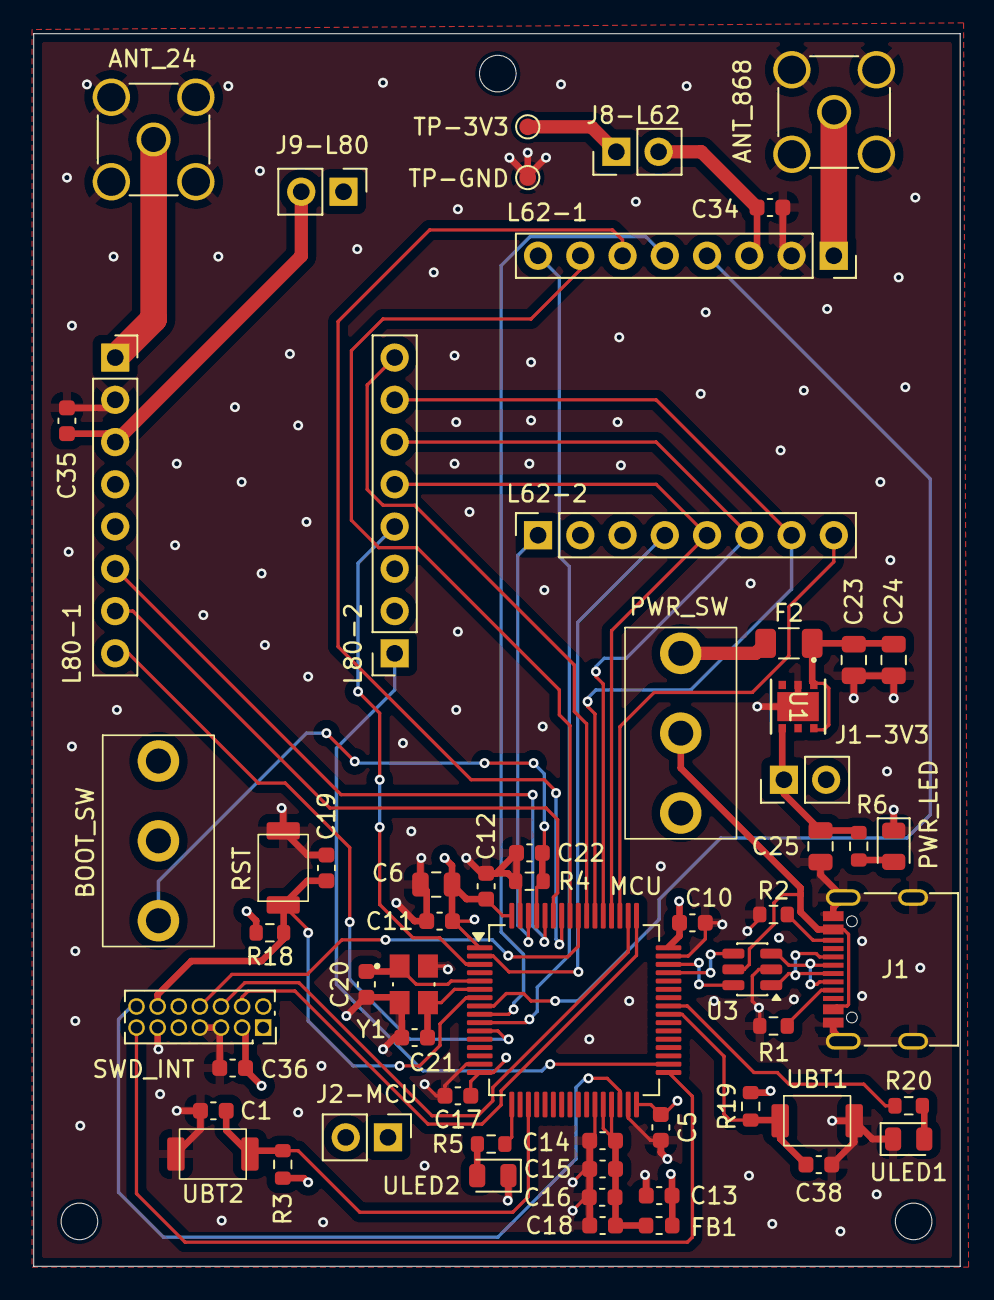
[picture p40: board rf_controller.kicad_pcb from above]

Board: 4 copper layers, 55.7 x 74.1 mm, 63 parts (0 on the bottom side), 51 nets.

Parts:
ANT_24: 2.4GHz antenna; SMA_Amphenol_901-144_Vertical
ANT_868: 868MHz antenna; SMA_Amphenol_901-144_Vertical
BOOT_SW: SW_SPDT; SHOU HAN SS12D10G5
C1, C5, C10, C11, C12, C15, C17, C19, C22, C34, C35, C36, C38: 100nF; C_0603_1608Metric
C6: 4u7F; C_0805_2012Metric
C13, C16, C18: 1uF; C_0603_1608Metric
C14: 10nF; C_0603_1608Metric
C20, C21: 12pF; C_0603_1608Metric
C23: 22uF; C_0805_2012Metric
C24, C25: 1uF; C_0805_2012Metric
F2: 500mA; Fuse_1206_3216Metric
FB1: 120R; L_0603_1608Metric
H1, H2, H3: MountingHole; MountingHole_2.2mm_M2
J1: USB_C_Receptacle_USB2.0_16P; USB_C_Receptacle_G-Switch_GT-USB-7010ASV
J1-3V3, J2-MCU, J8-L62, J9-L80: Conn_01x02; PinHeader_1x02_P2.54mm_Vertical
L62-1: LAMBDA62; PinSocket_1x08_P2.54mm_Vertical
L62-2, L80-2: Conn_01x08_Socket; PinSocket_1x08_P2.54mm_Vertical
L80-1: LAMBDA80; PinSocket_1x08_P2.54mm_Vertical
MCU: STM32G474RET6; LQFP-64_10x10mm_P0.5mm
PWR_LED: PWR LED; LED_0805_2012Metric
PWR_SW: SW_SPDT; SHOU HAN SS12D10G5
R1, R2: 5k1R; R_0603_1608Metric
R3, R4, R18, R19: 10kR; R_0603_1608Metric
R5, R6, R20: 220R; R_0603_1608Metric
RST: SW_Push; hanxia HX 3x4x2-2P-1.6N TACTILE SWITCH
SWD_INT: SWD interface; PinSocket_2x07_P1.27mm_Vertical
TP-3V3: TestPoint; TestPoint_Pad_D1.0mm
TP-GND: TestPoint; TestPoint_Pad_D1.0mm
U1: LDL112PV33R; DFN_2PV33R_STM
U3: USBLC6-2SC6; SOT-23-6
UBT1, UBT2: SW_Push; hanxia HX 3x4x2-2P-1.6N TACTILE SWITCH
ULED1, ULED2: PWR LED; LED_0805_2012Metric
Y1: 16MHz; XTAL_ABM8G-16.000MHZ-4Y-T3

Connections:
+3V3: BOOT_SW.2 (B), C36.2, J1-3V3.2, J2-MCU.2, J8-L62.1, J9-L80.1, R3.1, R18.2, R19.2, SWD_INT.3, TP-3V3.1
+3V3A: C14.1, C15.1, C16.1, C18.1, FB1.1, MCU.28 (VREF+), MCU.29 (VDDA)
/BOOT0: BOOT_SW.3 (C), C22.1, MCU.61 (PB8), R4.1
/CONN_D+: J1.A6 (D+), J1.B6 (D+), U3.1 (I/O1)
/CONN_D-: J1.A7 (D-), J1.B7 (D-), U3.3 (I/O2)
/L62_ANT: ANT_868.1 (In), L62-1.1
/L62_BUSY: L62-1.6, MCU.58 (PB5)
/L62_CS: L62-2.8, MCU.51 (PA15)
/L62_DIO1: L62-1.7, MCU.57 (PB4)
/L62_DIO2: L62-1.8, MCU.10 (PC2)
/L62_DIO3: L62-2.1, MCU.62 (PB9)
/L62_RST: L62-2.4, MCU.2 (PC13)
/L62_RXSW: L62-1.4, MCU.8 (PC0)
/L62_TXSW: L62-1.5, MCU.9 (PC1)
/L62_VCC: C34.2, J8-L62.2, L62-1.3
/L80_ANT: ANT_24.1 (In), L80-1.1
/L80_BUSY: L80-1.6, MCU.60 (PB7)
/L80_CS: L80-2.8, MCU.55 (PD2)
/L80_DIO1: L80-1.7, MCU.59 (PB6)
/L80_DIO2: L80-1.8, MCU.11 (PC3)
/L80_DIO3: L80-2.1, MCU.34 (PB12)
/L80_RST: L80-2.4, MCU.3 (PC14)
/L80_VCC: C35.2, J9-L80.2, L80-1.3
/NRST: C19.1, MCU.7 (PG10), R18.1, RST.2, SWD_INT.12
/SPI3_MISO: L62-2.6, L80-2.6, MCU.53 (PC11)
/SPI3_MOSI: L62-2.7, L80-2.7, MCU.54 (PC12)
/SPI3_SCK: L62-2.5, L80-2.5, MCU.52 (PC10)
/SWCLK: MCU.50 (PA14), SWD_INT.6
/SWDIO: MCU.49 (PA13), SWD_INT.4
/SWO: MCU.56 (PB3), SWD_INT.8
/USB_D+: MCU.46 (PA12), U3.6 (I/O1)
/USB_D-: MCU.45 (PA11), U3.4 (I/O2)
/USB_VBUS: J1.A4 (VBUS), J1.A9 (VBUS), J1.B4 (VBUS), J1.B9 (VBUS), PWR_SW.2 (B), U3.5 (VBUS)
/VCC-MCU: C5.1, C6.1, C10.1, C11.1, C12.1, C13.1, C17.1, FB1.2, J2-MCU.1, MCU.1 (VBAT), MCU.16 (VDD), MCU.32 (VDD), MCU.48 (VDD), MCU.64 (VDD)
/VCP_RX: MCU.33 (PB11), SWD_INT.13
/VCP_TX: MCU.30 (PB10), SWD_INT.14
GND: ANT_24.2 (Ext), ANT_868.2 (Ext), C1.2, C5.2, C6.2, C10.2, C11.2, C12.2, C13.2, C14.2, C15.2, C16.2, C17.2, C18.2, C19.2, C20.2, C21.2, C22.2, C23.2, C24.2, C25.2, C34.1, C35.1, C36.1, C38.2, J1.A1 (GND), J1.A12 (GND), J1.B1 (GND), J1.B12 (GND), J1.S1 (SHIELD), L62-1.2, L80-1.2, MCU.15 (VSS), MCU.27 (VSSA), MCU.31 (VSS), MCU.47 (VSS), MCU.63 (VSS), PWR_LED.1 (K), R1.1, R2.1, R4.2, RST.1, SWD_INT.5, SWD_INT.7, SWD_INT.11, TP-GND.1, U1.2 (GND), U1.7 (EPAD), U3.2 (GND), UBT1.1, UBT2.1, ULED1.1 (K), ULED2.1 (K), Y1.2 (GND), Y1.4 (GND)
unnamed: C25.1, J1-3V3.1, R6.1, U1.4 (VOUT)
unnamed: J1.A5 (CC1), R1.2
unnamed: J1.B5 (CC2), R2.2
unnamed: MCU.17 (PA3), R5.2
unnamed: C1.1, MCU.19 (PA5), R3.2, UBT2.2
unnamed: C38.1, MCU.40 (PC8), R19.1, UBT1.2
unnamed: MCU.41 (PC9), R20.2
unnamed: C20.1, MCU.5 (PF0), Y1.1
unnamed: C21.1, MCU.6 (PF1), Y1.3
unnamed: PWR_LED.2 (A), R6.2
unnamed: F2.1, PWR_SW.1 (A)
unnamed: C23.1, C24.1, F2.2, U1.1 (EN), U1.6 (VIN)
unnamed: R20.1, ULED1.2 (A)
unnamed: R5.1, ULED2.2 (A)

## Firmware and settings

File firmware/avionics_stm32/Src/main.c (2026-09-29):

#include "main.h"


TS_Vec3 lsm_accbuff[LSM6_FIFO_READNUM];
TS_Vec3 lsm_gyrbuff[LSM6_FIFO_READNUM];
float lsm_data_time = 0.0f;

TS_Vec3 adxl_accbuff[ADXL_FIFO_READNUM];
float adxl_data_time = 0.0f;

TS_PressTemp bmp_buff[BMP_FIFO_READNUM];
float bmp_data_time = 0.0f;

TS_Vec3 mmc_buff;
float mmc_data_time = 0.0f;

TS_GPS m10s_buff;



FlightState_t CurrentFlightState = FLIGHT_STATE_PAD;



void ReadLSM6DSRTask(void *param) {
	(void) param;

    while (1) {
        if (ulTaskNotifyTake(pdTRUE, portMAX_DELAY)) {
			if (xSemaphoreTake(SPIAccMutex, pdMS_TO_TICKS(20)) != pdTRUE) {
				printf("[ERROR] LSM6DSR read timed out due to unreleased SPI mutex\n");
				continue;
			}

			LSM6DSR_ReadFIFOData(&hspi1_acc, lsm_accbuff, lsm_gyrbuff, LSM6_FIFO_READNUM, lsm_data_time);

			xSemaphoreGive(SPIAccMutex);

			SensorData data;

			for (int i = 0; i < LSM6_FIFO_READNUM; i++) {
				// Calibrate reading
				CalVectorCentDist(&lsm_accbuff[i], LACC_CAL_CENT, LACC_CAL_DIST);

				data.type = SENSOR_DATA_LRACC;
				data.data.tsvec3 = lsm_accbuff[i];

				if (xQueueSend(DataLogQueue, &data, pdMS_TO_TICKS(0)) != pdPASS) {
					printf("[ERROR] Data log queue full\n");
				}

				if (xQueueSend(FusionQueue, &data, pdMS_TO_TICKS(0)) != pdPASS) {
					printf("[ERROR] Fusion queue full\n");
				}


				// Calibrate reading
				CalVectorCent(&lsm_gyrbuff[i], GYR_CAL_CENT);

				data.type = SENSOR_DATA_GYR;
				data.data.tsvec3 = lsm_gyrbuff[i];

				if (xQueueSend(DataLogQueue, &data, pdMS_TO_TICKS(0)) != pdPASS) {
					printf("[ERROR] Data log queue full\n");
				}

				if (xQueueSend(FusionQueue, &data, pdMS_TO_TICKS(0)) != pdPASS) {
					printf("[ERROR] Fusion queue full\n");
				}
			}
        }
    }
}


void ReadADXL375Task(void *param) {
	(void) param;

    while (1) {
        if (ulTaskNotifyTake(pdTRUE, portMAX_DELAY)) {
			if (xSemaphoreTake(SPIAccMutex, pdMS_TO_TICKS(20)) != pdTRUE) {
				printf("[ERROR] ADXL375 read timed out due to unreleased SPI mutex\n");
				continue;
			}

			ADXL375_ReadFIFOData(&hspi1_acc, adxl_accbuff, ADXL_FIFO_READNUM, adxl_data_time);

			xSemaphoreGive(SPIAccMutex);

			SensorData data;

			for (int i = 0; i < ADXL_FIFO_READNUM; i++) {
				// Calibrate reading
				CalVectorCentDist(&adxl_accbuff[i], HACC_CAL_CENT, HACC_CAL_DIST);

				data.type = SENSOR_DATA_HRACC;
				data.data.tsvec3 = adxl_accbuff[i];

				if (xQueueSend(DataLogQueue, &data, pdMS_TO_TICKS(0)) != pdPASS) {
					printf("[ERROR] Data log queue full\n");
				}

				if (xQueueSend(FusionQueue, &data, pdMS_TO_TICKS(0)) != pdPASS) {
					printf("[ERROR] Fusion queue full\n");
				}
			}
        }
    }
}


void ReadBMP581Task(void *param) {
	(void) param;

    while (1) {
        if (ulTaskNotifyTake(pdTRUE, portMAX_DELAY)) {
			if (xSemaphoreTake(I2CMutex, pdMS_TO_TICKS(20)) != pdTRUE) {
				printf("[ERROR] BMP581 read timed out due to unreleased I2C mutex\n");
				continue;
			}

			BMP581_ReadFIFOData(&hi2c, bmp_buff, BMP_FIFO_READNUM, bmp_data_time);

			xSemaphoreGive(I2CMutex);

			SensorData data;

			for (int i = 0; i < BMP_FIFO_READNUM; i++) {
				data.type = SENSOR_DATA_PRSTMP;
				data.data.tsprstmp = bmp_buff[i];

				if (!SettingHome) {   // Only push to log queue if not being used to set home
					if (xQueueSend(DataLogQueue, &data, pdMS_TO_TICKS(0)) != pdPASS) {
						printf("[ERROR] Data log queue full\n");
					}
				}

				if (xQueueSend(FusionQueue, &data, pdMS_TO_TICKS(0)) != pdPASS) {
					printf("[ERROR] Fusion queue full\n");
				}
			}
        }
    }
}


void ReadMMC5983Task(void *param) {
	(void) param;

    while (1) {
        if (ulTaskNotifyTake(pdTRUE, portMAX_DELAY)) {
			if (xSemaphoreTake(I2CMutex, pdMS_TO_TICKS(20)) != pdTRUE) {
				printf("[ERROR] MMC5983 read timed out due to unreleased I2C mutex\n");
				continue;
			}

			MMC5983MA_ReadData(&hi2c, &mmc_buff, mmc_data_time);

			xSemaphoreGive(I2CMutex);

			// Calibrate reading
			CalVectorCentDist(&mmc_buff, MAG_CAL_CENT, MAG_CAL_DIST);

			SensorData data;
			data.type = SENSOR_DATA_MAG;
			data.data.tsvec3 = mmc_buff;

			if (xQueueSend(DataLogQueue, &data, pdMS_TO_TICKS(0)) != pdPASS) {
				printf("[ERROR] Data log queue full\n");
			}

			if (xQueueSend(FusionQueue, &data, pdMS_TO_TICKS(0)) != pdPASS) {
				printf("[ERROR] Fusion queue full\n");
			}
        }
    }
}


void ReadM10STask(void *param) {
	(void) param;

	UBXPacket pkt;

    while (1) {
        if (ulTaskNotifyTake(pdTRUE, portMAX_DELAY)) {
			if (xSemaphoreTake(I2CMutex, pdMS_TO_TICKS(20)) != pdTRUE) {
				printf("[ERROR] M10S read timed out due to unreleased I2C mutex\n");
				continue;
			}

			uint16_t bytes_available = MAXM10S_GetAvailableBytes(&hi2c);
			if (bytes_available == 0) {
				xSemaphoreGive(I2CMutex);
				continue;
			}

			uint8_t i2c_data[bytes_available];

			if (!MAXM10S_ReadStream(&hi2c, i2c_data, bytes_available)) {
				xSemaphoreGive(I2CMutex);
				continue;
			}

			xSemaphoreGive(I2CMutex);

			uint16_t readoffset = 0;
			while (readoffset < bytes_available) {
				if (MAXM10S_ParseUBXStream(i2c_data, bytes_available, &readoffset, &pkt)) {
					if (pkt.class == 0x01 && pkt.id == 0x07) {
						MAXM10S_ExtractPVTData(&pkt, &m10s_buff);

						SensorData data;
						data.type = SENSOR_DATA_GPS;
						data.data.tsgps = m10s_buff;

						if (!SettingHome) {   // Only push to log queue if not being used to set home
							if (xQueueSend(DataLogQueue, &data, pdMS_TO_TICKS(0)) != pdPASS) {
								printf("[ERROR] Data log queue full\n");
							}
						}

						if (xQueueSend(FusionQueue, &data, pdMS_TO_TICKS(0)) != pdPASS) {
							printf("[ERROR] Fusion queue full\n");
						}
					}
				}
			}
        }
    }
}


void TriggerDataCollectionTask(void *param) {
	(void) param;

    while (1) {
        if (ulTaskNotifyTake(pdTRUE, portMAX_DELAY)) {
        	if (DataCollectionEnabled) {   // When starting data collection, first wipe stored flight data and start the logging timer
        		printf("[INFO] Starting data logging\n");

        		// Clear queues
        		xQueueReset(DataLogQueue);
        		xQueueReset(FusionQueue);

    			if (xSemaphoreTake(SPIFlashMutex, pdMS_TO_TICKS(20)) == pdTRUE) {
    				printf("[INFO] Wiping previous flight data\n");

    				ULED1_ON

    				W25Q_EraseFlightData();
    				xSemaphoreGive(SPIFlashMutex);

    				ULED1_OFF
    			} else {
    				printf("[ERROR] Could not wipe previous flight data due to unreleased SPI mutex\n");
    			}

    			xTimerStart(LogDataTimer, 0);
        	} else {   // When stopping data collection, stop the logging timer and trigger a final write
        		printf("[INFO] Stopping data logging\n");

        		xTimerStop(LogDataTimer, 0);
        		xTaskNotifyGive(LogDataTaskNotif);
        	}

        	SetDataCollectionEnabled(DataCollectionEnabled);

        	xSemaphoreGive(DataReadySemphr);
        }
    }
}


void LogDataTask(void *param) {
	(void) param;

	SensorData datapkt;
	uint8_t WriteBuff[FLASH_BUFFER_LEN];
	uint16_t WriteBuffPos = 8;   // First 8 bytes reserved for sync word and header
	uint8_t WriteBuffReadings = 0;

	// Preload sync word
	for (int i = 3; i >= 0; i--) {
		WriteBuff[3 - i] = (uint8_t)((W25Q_DATA_SYNC_WORD >> (i * 8)) & 0xFF);
	}

    while (1) {
    	if (xQueueReceive(DataLogQueue, &datapkt, pdMS_TO_TICKS(5)) == pdPASS) {   // Try to receive any queued sensor data packets
    		// If a packet is received, serialise it and append it to the write buffer
    		switch (datapkt.type) {
    			case SENSOR_DATA_LRACC:
    				LSM6DSR_AppendLogPacketAcc(WriteBuff, &WriteBuffPos, FLASH_BUFFER_LEN, &datapkt.data.tsvec3, 1);
    				break;
    			case SENSOR_DATA_GYR:
    				LSM6DSR_AppendLogPacketGyr(WriteBuff, &WriteBuffPos, FLASH_BUFFER_LEN, &datapkt.data.tsvec3, 1);
    				break;
    			case SENSOR_DATA_HRACC:
    				ADXL375_AppendLogPacket(WriteBuff, &WriteBuffPos, FLASH_BUFFER_LEN, &datapkt.data.tsvec3, 1);
    				break;
    			case SENSOR_DATA_MAG:
    				MMC5983MA_AppendLogPacket(WriteBuff, &WriteBuffPos, FLASH_BUFFER_LEN, &datapkt.data.tsvec3, 1);
    				break;
    			case SENSOR_DATA_PRSTMP:
    				BMP581_AppendLogPacket(WriteBuff, &WriteBuffPos, FLASH_BUFFER_LEN, &datapkt.data.tsprstmp, 1);
    				break;
    			case SENSOR_DATA_GPS:
    				MAXM10S_AppendLogPacket(WriteBuff, &WriteBuffPos, FLASH_BUFFER_LEN, &datapkt.data.tsgps, 1);
    				break;
    		}
    		WriteBuffReadings++;
    	}

        if (ulTaskNotifyTake(pdTRUE, pdMS_TO_TICKS(0))) {   // Log the data once triggered
        	ULED1_TOGGLE

        	// Ready CRC unit
        	CRC->CR |= CRC_CR_RESET;
        	volatile uint8_t *CRC_DR8 = (volatile uint8_t *)&CRC->DR;

    		// Calculate CRC for all bytes after header
    		for (uint16_t i = 8; i < WriteBuffPos; i++) {
    			*CRC_DR8 = WriteBuff[i];
    		}

    		// Load header into byte positions 4-7
    		WriteBuff[4] = WriteBuffReadings;
    		WriteBuff[5] = (uint8_t)((WriteBuffPos - 8) >> 8);
    		WriteBuff[6] = (uint8_t)(WriteBuffPos - 8);
    		WriteBuff[7] = (uint8_t)(CRC->DR);


			if (xSemaphoreTake(SPIFlashMutex, pdMS_TO_TICKS(20)) != pdTRUE) {
				printf("[ERROR] Data logging timed out due to unreleased SPI mutex\n");
				continue;
			}

    		// Write full buffer to flash
    		W25Q_WriteAppendData(WriteBuff, WriteBuffPos);

    		xSemaphoreGive(SPIFlashMutex);

    		printf("[INFO] Logged %i readings\n", WriteBuffReadings);

    		// Reset end point but leave space for header
    		WriteBuffPos = 8;
    		WriteBuffReadings = 0;
        }
    }
}


void ReadIncomingLAMBDA80(void *param) {
	(void) param;

    while (1) {
        if (ulTaskNotifyTake(pdTRUE, portMAX_DELAY)) {
			if (xSemaphoreTake(SPIRfMutex, pdMS_TO_TICKS(50)) != pdTRUE) {
				printf("[ERROR] LAMBDA80 read timed out due to unreleased SPI mutex\n");
				return;
			}

			// Store interrupt status
			uint16_t irq = LAMBDA80_GetIRQStatus(&hspi3_rf, false);

			// Clear Rx interrupt
			LAMBDA80_ClearIRQ(&hspi3_rf, 0xFFFF, false);

			// Read the raw bytes from the radio buffer
			uint8_t len = 0;
			uint8_t start = 0;
			LAMBDA80_GetRxBufferStatus(&hspi3_rf, &len, &start, false);

			uint8_t buff[256];
			LAMBDA80_ReadBuffer(&hspi3_rf, buff, start, len, false);

			xSemaphoreGive(SPIRfMutex);

			// Decode raw bytes into a net packet
			NetPacket pkt;
			DecodeNetPacket(&pkt, buff, len);

			pkt.pktstatus = 1;   // Set 2.4GHz freq source bit
			pkt.pktstatus |= ((irq >> 5) & 2);   // Set CRC error bit

			// Place into the radio response queue
			if (xQueueSend(RadioQueue, &pkt, pdMS_TO_TICKS(10)) != pdPASS) {
				printf("[ERROR] Radio response queue full\n");
			}
        }
    }
}


void ReadIncomingLAMBDA62(void *param) {
	(void) param;

    while (1) {
        if (ulTaskNotifyTake(pdTRUE, portMAX_DELAY)) {
			if (xSemaphoreTake(SPIRfMutex, pdMS_TO_TICKS(50)) != pdTRUE) {
				printf("[ERROR] LAMBDA62 read timed out due to unreleased SPI mutex\n");
				return;
			}

			// Store interrupt status
			uint16_t irq = LAMBDA62_GetIRQStatus(&hspi3_rf, false);

			// Clear Rx interrupt
			LAMBDA62_ClearIRQ(&hspi3_rf, 0xFFFF, false);

			// Read the raw bytes from the radio buffer
			uint8_t len = 0;
			uint8_t start = 0;
			LAMBDA62_GetRxBufferStatus(&hspi3_rf, &len, &start, false);

			uint8_t buff[256];
			LAMBDA62_ReadBuffer(&hspi3_rf, buff, start, len, false);

			xSemaphoreGive(SPIRfMutex);

			// Decode raw bytes into a net packet
			NetPacket pkt;
			DecodeNetPacket(&pkt, buff, len);

			pkt.pktstatus = 0;   // Set 868MHz freq source bit
			pkt.pktstatus |= ((irq >> 5) & 2);   // Set CRC error bit

			// Place into the radio response queue
			if (xQueueSend(RadioQueue, &pkt, pdMS_TO_TICKS(10)) != pdPASS) {
				printf("[ERROR] Radio response queue full\n");
			}
        }
    }
}


void TransactionManagerTask(void *param) {
	(void) param;

	// State to function mapping table
	static const TMStateHandler TMStateTable[TM_NUM_STATES] = {
	    [TM_STATE_IDLE] = HandleStateIdle,
		[TM_DISC_CMD] = HandleStateDiscoveryCmd,
		[TM_PKTTEST_CMD] = HandleStatePktTestCmd,
		[TM_DATARNG_CMD] = HandleStateDataRangeCmd,
		[TM_TRSMT_DATA_CMD] = HandleStateTransmitDataCmd,
		[TM_TELEMETRY_CMD] = HandleStateTelemetryCmd,
		[TM_SETHOME] = HandleStateSetHomeCmd
	};

    TMState currState = TM_STATE_IDLE;
    NetPacket currRadResp;

    // Continuously execute the function that maps to the current state and update the current state
    while (1) {
    	currState = TMStateTable[currState](&currRadResp);
    }
}


TMState HandleStateIdle(NetPacket* pkt) {
	// Wait for a command to arrive over radio
	if (xQueueReceive(RadioQueue, pkt, portMAX_DELAY) == pdPASS) {
		if (pkt->type == NET_MTYPE_DISCOVERY) { return TM_DISC_CMD; }
		if (pkt->type == NET_MTYPE_PKTTEST) { return TM_PKTTEST_CMD; }
		if (pkt->type == NET_MTYPE_GET_DATA_RANGE) { return TM_DATARNG_CMD; }
		if (pkt->type == NET_MTYPE_TRSMT_DATA) { return TM_TRSMT_DATA_CMD; }
		if (pkt->type == NET_MTYPE_TELEMETRY_START) { return TM_TELEMETRY_CMD; }
		if (pkt->type == NET_MTYPE_SETHOME) { return TM_SETHOME; }
	}
	return TM_STATE_IDLE;
}
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
int main(void) {
	// System init
	HAL_Init();

	SystemClockConfig();
	InitialiseGPIO();
	InitialiseI2C();
	InitialiseSPI();
	InitialiseCRC();
	InitialiseTimers();

	HAL_Delay(100);

	// Initialise RF modules
	InitialiseLAMBDA62FSK(&hspi3_rf, true);
	LAMBDA62_SetPacketParamsFSK(&hspi3_rf, 32, 5, 64, 0, true, NET_PACKET_MAXLEN, 2, false, true);
	LAMBDA62_SetRx(&hspi3_rf, 0xFFFFFF, true);


	InitialiseLAMBDA80(&hspi3_rf, true);
	LAMBDA80_SetMode_Telemetry(&hspi3_rf, true);


	// Initialise storage
	if (!InitialiseW25Q()) { Error_Handler(); }


	// Initialise sensors
	if (!InitialiseLSM6DSR(&hspi1_acc, LSM6_FIFO_READNUM, true)) { Error_Handler(); }
	if (!InitialiseADXL375(&hspi1_acc, ADXL_FIFO_READNUM, true)) { Error_Handler(); }
	if (!InitialiseBMP581(&hi2c, BMP_FIFO_READNUM, true)) { Error_Handler(); }
	if (!InitialiseMMC5983MA(&hi2c, true)) { Error_Handler(); }
	if (!InitialiseMAXM10S(&hi2c, true)) { Error_Handler(); }


	__enable_irq();


	// Initialise FreeRTOS objects
	RadioQueue = xQueueCreate(5, sizeof(NetPacket));
	if (RadioQueue == NULL) { Error_Handler(); }

	DataLogQueue = xQueueCreate(25, sizeof(SensorData));
	if (DataLogQueue == NULL) { Error_Handler(); }

	FusionQueue = xQueueCreate(25, sizeof(SensorData));
	if (FusionQueue == NULL) { Error_Handler(); }

	SPIRfMutex = xSemaphoreCreateMutex();
	if (SPIRfMutex == NULL) { Error_Handler(); }

	SPIAccMutex = xSemaphoreCreateMutex();
	if (SPIAccMutex == NULL) { Error_Handler(); }

	SPIFlashMutex = xSemaphoreCreateMutex();
	if (SPIFlashMutex == NULL) { Error_Handler(); }

	I2CMutex = xSemaphoreCreateMutex();
	if (I2CMutex == NULL) { Error_Handler(); }

	LAMBDA80TxSemphr = xSemaphoreCreateBinary();
	if (LAMBDA80TxSemphr == NULL) { Error_Handler(); }

	LAMBDA62TxSemphr = xSemaphoreCreateBinary();
	if (LAMBDA62TxSemphr == NULL) { Error_Handler(); }

	DataReadySemphr = xSemaphoreCreateBinary();
	if (DataReadySemphr == NULL) { Error_Handler(); }


	// Create tasks
    xTaskCreate(ReadIncomingLAMBDA80, "LAMBDA80-Receive", 1024, NULL, 4, &LAMBDA80RxTaskNotif);
    xTaskCreate(ReadIncomingLAMBDA62, "LAMBDA62-Receive", 1024, NULL, 4, &LAMBDA62RxTaskNotif);
    xTaskCreate(TransactionManagerTask, "Transaction-Manager", 4096, NULL, 1, NULL);

    xTaskCreate(ReadLSM6DSRTask, "Read-LSM6DSR", 512, NULL, 6, &LSM6DSRReadTaskNotif);
    xTaskCreate(ReadADXL375Task, "Read-ADXL375", 512, NULL, 6, &ADXL375ReadTaskNotif);
    xTaskCreate(ReadBMP581Task, "Read-BMP581", 512, NULL, 5, &BMP581ReadTaskNotif);
    xTaskCreate(ReadMMC5983Task, "Read-MMC5983", 512, NULL, 5, &MMC5983ReadTaskNotif);
    xTaskCreate(ReadM10STask, "Read-M10S", 512, NULL, 5, &M10SReadTaskNotif);

    xTaskCreate(TriggerDataCollectionTask, "Trigger-Data-Collection", 512, NULL, 1, &DataCollectionTaskNotif);

    xTaskCreate(LogDataTask, "Log-Data", 1024, NULL, 3, &LogDataTaskNotif);

    xTaskCreate(SensorFusionTask, "Fuse-Data", 1024, NULL, 1, &FusionTaskHandle);
    xTaskCreate(FlightControlTask, "Flight-Control", 1024, NULL, 4, NULL);


    // Set up periodic polling of MAX-M10S module (twice expected data rate)
    M10SPollTimer = xTimerCreate("M10SPollTimer", pdMS_TO_TICKS(250), pdTRUE, (void *)0, PrimeM10SPoll);
    xTimerStart(M10SPollTimer, 0);

    // Set up periodic data logging to flash
    LogDataTimer = xTimerCreate("LogDataTimer", pdMS_TO_TICKS(100), pdTRUE, (void *)0, PrimeLogData);

    printf("INIT\n");

    vTaskStartScheduler();

	while (1) {}
}




void TIM2_IRQHandler() {
	if (TIM2->SR & TIM_SR_UIF) {
		TIM2->SR &= ~TIM_SR_UIF;   // Clear interrupt flag
	}
}


void PrimeM10SPoll(TimerHandle_t Timer) {
	xTaskNotifyGive(M10SReadTaskNotif);
}


void PrimeLogData(TimerHandle_t Timer) {
	xTaskNotifyGive(LogDataTaskNotif);
}



void SetDataCollectionEnabled(bool Collect) {
	if (Collect) {
		if (xSemaphoreTake(I2CMutex, pdMS_TO_TICKS(100)) == pdTRUE) {
			// Wake the slow sensors first
			MAXM10S_SetDataOutput(&hi2c, true, false);
			MMC5983MA_SetMeasurement(&hi2c, MMC_DR_10HZ);
			BMP581_SetMeasure(&hi2c, BMP_DR_10HZ);

			xSemaphoreGive(I2CMutex);
		} else {
			printf("[ERROR] Slow sensor startup timed out due to unreleased I2C mutex\n");
		}

		if (xSemaphoreTake(SPIAccMutex, pdMS_TO_TICKS(100)) != pdTRUE) {
			printf("[ERROR] Fast sensor startup timed out due to unreleased SPI mutex\n");
			return;
		}

		// Then the fast sensors
		ADXL375_SetMeasure(&hspi1_acc);
		LSM6DSR_SetMeasurementMode(&hspi1_acc, LSM6_DR_104HZ, LSM6_ACCRNG_8G, LSM6_ACCFILT_FS, LSM6_DR_104HZ, LSM6_GYRRNG_2000DPS);

		xSemaphoreGive(SPIAccMutex);

		xTimerStart(M10SPollTimer, 0);
	} else {
		xTimerStop(M10SPollTimer, 0);

		if (xSemaphoreTake(SPIAccMutex, pdMS_TO_TICKS(100)) == pdTRUE) {
			// Stop the fast sensors first
			LSM6DSR_SetMeasurementMode(&hspi1_acc, LSM6_DR_NONE, LSM6_ACCRNG_8G, LSM6_ACCFILT_FS, LSM6_DR_NONE, LSM6_GYRRNG_2000DPS);
			ADXL375_SetStandby(&hspi1_acc);

			xSemaphoreGive(SPIAccMutex);
		} else {
			printf("[ERROR] Fast sensor sleep timed out due to unreleased SPI mutex\n");
		}

		if (xSemaphoreTake(I2CMutex, pdMS_TO_TICKS(100)) != pdTRUE) {
			printf("[ERROR] Slow sensor sleep timed out due to unreleased I2C mutex\n");
			return;
		}

		// Then the slow sensors
		BMP581_SetStandby(&hi2c);
		MMC5983MA_SetMeasurement(&hi2c, MMC_DR_NONE);
		MAXM10S_SetDataOutput(&hi2c, false, false);

		xSemaphoreGive(I2CMutex);
	}
}





// Initialisation functions
void SystemClockConfig(void) {
    RCC_OscInitTypeDef RCC_OscInitStruct = {0};
    RCC_ClkInitTypeDef RCC_ClkInitStruct = {0};

    // Configure main internal regulator output voltage
    __HAL_RCC_PWR_CLK_ENABLE();
    HAL_PWREx_ControlVoltageScaling(PWR_REGULATOR_VOLTAGE_SCALE1_BOOST);

    // Initialise the RCC Oscillators
    RCC_OscInitStruct.OscillatorType = RCC_OSCILLATORTYPE_HSE;
    RCC_OscInitStruct.HSEState = RCC_HSE_ON;
    RCC_OscInitStruct.PLL.PLLState = RCC_PLL_ON;
    RCC_OscInitStruct.PLL.PLLSource = RCC_PLLSOURCE_HSE;
    RCC_OscInitStruct.PLL.PLLM = RCC_PLLM_DIV4;
    RCC_OscInitStruct.PLL.PLLN = 85;
    RCC_OscInitStruct.PLL.PLLP = RCC_PLLP_DIV2;
    RCC_OscInitStruct.PLL.PLLQ = RCC_PLLQ_DIV2;
    RCC_OscInitStruct.PLL.PLLR = RCC_PLLR_DIV2;

    if (HAL_RCC_OscConfig(&RCC_OscInitStruct) != HAL_OK) { Error_Handler(); }

    // Initialise CPU, AHB and APB bus clocks
    RCC_ClkInitStruct.ClockType = RCC_CLOCKTYPE_HCLK | RCC_CLOCKTYPE_SYSCLK | RCC_CLOCKTYPE_PCLK1 | RCC_CLOCKTYPE_PCLK2;
    RCC_ClkInitStruct.SYSCLKSource = RCC_SYSCLKSOURCE_PLLCLK;
    RCC_ClkInitStruct.AHBCLKDivider = RCC_SYSCLK_DIV1;
    RCC_ClkInitStruct.APB1CLKDivider = RCC_HCLK_DIV1;
    RCC_ClkInitStruct.APB2CLKDivider = RCC_HCLK_DIV1;

    if (HAL_RCC_ClockConfig(&RCC_ClkInitStruct, FLASH_LATENCY_4) != HAL_OK) { Error_Handler(); }
}

void InitialiseI2C() {
	// Set I2C clock source
	RCC_PeriphCLKInitTypeDef PeriphClkInit = {0};
    PeriphClkInit.PeriphClockSelection = RCC_PERIPHCLK_I2C2;
    PeriphClkInit.I2c2ClockSelection = RCC_I2C2CLKSOURCE_PCLK1;
    if (HAL_RCCEx_PeriphCLKConfig(&PeriphClkInit) != HAL_OK) { Error_Handler(); }

	// Turn on port A clock
	__HAL_RCC_GPIOA_CLK_ENABLE();

	// Configure alternate function pins
	GPIO_InitTypeDef GPIO_InitStruct = {0};
	GPIO_InitStruct.Pin = GPIO_PIN_8 | GPIO_PIN_9;
	GPIO_InitStruct.Mode = GPIO_MODE_AF_OD;
	GPIO_InitStruct.Pull = GPIO_NOPULL;
	GPIO_InitStruct.Speed = GPIO_SPEED_FREQ_LOW;
	GPIO_InitStruct.Alternate = GPIO_AF4_I2C2;
	HAL_GPIO_Init(GPIOA, &GPIO_InitStruct);

	// Turn on I2C clock
	__HAL_RCC_I2C2_CLK_ENABLE();

	// Initialise I2C2 (magnetometer, barometer, GPS)
	hi2c.Instance = I2C2;
	hi2c.Init.Timing = 0x40B285C2;   // PRESC (0), SCLDEL (1-2), SDADEL (3), SCLH (4-5), SCLL (6-7)
	hi2c.Init.OwnAddress1 = 0;
	hi2c.Init.AddressingMode = I2C_ADDRESSINGMODE_7BIT;   // Standard 7-bit addressing
	hi2c.Init.DualAddressMode = I2C_DUALADDRESS_DISABLE;   // Disable dual addressing (reading two slaves simultaneously)
	hi2c.Init.OwnAddress2 = 0;
	hi2c.Init.OwnAddress2Masks = I2C_OA2_NOMASK;
	hi2c.Init.GeneralCallMode = I2C_GENERALCALL_DISABLE;   // Disable ability to respond to a broadcast
	hi2c.Init.NoStretchMode = I2C_NOSTRETCH_DISABLE;   // Allow slaves to hold the clock low to pause communication

	if (HAL_I2C_Init(&hi2c) != HAL_OK) { Error_Handler(); }

	// Turn on analogue filter
	if (HAL_I2CEx_ConfigAnalogFilter(&hi2c, I2C_ANALOGFILTER_ENABLE) != HAL_OK) { Error_Handler(); }

	// Turn off digital filter
	if (HAL_I2CEx_ConfigDigitalFilter(&hi2c, 0) != HAL_OK) { Error_Handler(); }
}
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

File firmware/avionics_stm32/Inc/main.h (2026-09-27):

#ifndef MAIN_H_
#define MAIN_H_

#include "stm32g4xx.h"
#include "FreeRTOS.h"
#include "task.h"
#include "queue.h"
#include "semphr.h"
#include "timers.h"

#include "pinconfig.h"
#include "adxl375.h"
#include "lsm6dsr.h"
#include "bmp581.h"
#include "mmc5983.h"
#include "m10s.h"
#include "w25q.h"
#include "lambda62.h"
#include "lambda80.h"

#include <math.h>
#include <stdint.h>
#include <stdbool.h>
#include <string.h>
#include <stdio.h>

#include "datatypes.h"
#include "misc.h"
#include "networking.h"

#include "fusion.h"


I2C_HandleTypeDef hi2c;
SPI_HandleTypeDef hspi1_acc;
SPI_HandleTypeDef hspi2_str;
SPI_HandleTypeDef hspi3_rf;


#define NET_ADDRESS NET_AVIONICS_ADDR

#define TELEMETRY_PERIOD_MS 100   // Minimum ms between each telemetry packet sent


// Task notifications
TaskHandle_t LAMBDA80RxTaskNotif = NULL;
TaskHandle_t LAMBDA62RxTaskNotif = NULL;
TaskHandle_t LSM6DSRReadTaskNotif = NULL;
TaskHandle_t ADXL375ReadTaskNotif = NULL;
TaskHandle_t BMP581ReadTaskNotif = NULL;
TaskHandle_t MMC5983ReadTaskNotif = NULL;
TaskHandle_t M10SReadTaskNotif = NULL;
TaskHandle_t DataCollectionTaskNotif = NULL;
TaskHandle_t LogDataTaskNotif = NULL;

TaskHandle_t FusionTaskHandle = NULL;

// Semaphores
SemaphoreHandle_t LAMBDA80TxSemphr = NULL;
SemaphoreHandle_t LAMBDA62TxSemphr = NULL;
SemaphoreHandle_t DataReadySemphr = NULL;

// Mutexes
SemaphoreHandle_t SPIRfMutex = NULL;
SemaphoreHandle_t SPIAccMutex = NULL;
SemaphoreHandle_t SPIFlashMutex = NULL;
SemaphoreHandle_t I2CMutex = NULL;

// Queue handles
QueueHandle_t RadioQueue;
QueueHandle_t DataLogQueue;
QueueHandle_t FusionQueue;

// Timers and callback functions
TimerHandle_t M10SPollTimer;
void PrimeM10SPoll(TimerHandle_t Timer);

TimerHandle_t LogDataTimer;
void PrimeLogData(TimerHandle_t Timer);


// Tasks
// Read from radio modules and push the packet onto the radio receive queue
// TODO Uses DMA transfers for packets above RADIO_PKTLEN_DMA_THRESH bytes long
#define RADIO_PKTLEN_DMA_THRESH 100

void ReadIncomingLAMBDA80(void *param);
void ReadIncomingLAMBDA62(void *param);

// Executes a state machine to handle all transaction types
void TransactionManagerTask(void *param);

/// Read from sensors when data is ready
void ReadLSM6DSRTask(void *param);
void ReadADXL375Task(void *param);
void ReadBMP581Task(void *param);
void ReadMMC5983Task(void *param);
void ReadM10STask(void *param);   // Must be polled as it doesn't have a ready interrupt

// Enable or disable data collection
bool DataCollectionEnabled = false;
void TriggerDataCollectionTask(void *param);

// Log data to flash storage
void LogDataTask(void *param);

// Fuse sensor data into 3D estimate
void SensorFusionTask(void *param);

// Keep track of what state of flight the unit is currently in
void FlightControlTask(void *param);

// Trigger the parachute system
void DeployParachute();


// States for the transaction manager state machine
typedef enum {
	TM_STATE_IDLE,
	TM_DISC_CMD,
	TM_PKTTEST_CMD,
	TM_DATARNG_CMD,
	TM_TRSMT_DATA_CMD,
	TM_TELEMETRY_CMD,
	TM_SETHOME,
    TM_NUM_STATES   // Not an actual state, just useful for getting the number of possible states
} TMState;

// Transaction manager state handler function signature
// All functions take in the most recent radio packet and return the state the transaction manager should transition to
typedef TMState (*TMStateHandler)(NetPacket* pkt);

// Transaction manager state handler functions
TMState HandleStateIdle(NetPacket* pkt);
TMState HandleStateDiscoveryCmd(NetPacket* pkt);
TMState HandleStatePktTestCmd(NetPacket* resp);
TMState HandleStateDataRangeCmd(NetPacket* resp);
TMState HandleStateTransmitDataCmd(NetPacket* resp);
TMState HandleStateTelemetryCmd(NetPacket* resp);
TMState HandleStateSetHomeCmd(NetPacket* resp);



// Sensor config
#define LSM6_FIFO_READNUM 4
#define ADXL_FIFO_READNUM 4
#define BMP_FIFO_READNUM 1

#define FLASH_BUFFER_LEN 1024

void SetDataCollectionEnabled(bool Collect);


// Samples needed for GPS and pressure to set home position. Home is set when both thresholds are met
#define SETHOME_MIN_GPS_SAMPLES 10
#define SETHOME_MIN_PRES_SAMPLES 30

bool SettingHome = false;   // For redirecting readings to home position calculation
bool HomePositionSet = false;   // Whether the home position has been initialised at least once since power on



// Flight stage state machine
typedef enum {
    FLIGHT_STATE_PAD,
    FLIGHT_STATE_BOOST,
    FLIGHT_STATE_COAST,
    FLIGHT_STATE_DESCENT,
    FLIGHT_STATE_LANDED
} FlightState_t;





// System initialisation
void SystemClockConfig(void);

void InitialiseGPIO();
void InitialiseI2C();
void InitialiseSPI();
void InitialiseCRC();
void InitialiseTimers();


// Error handling
void Error_Handler(void);


#endif /* MAIN_H_ */

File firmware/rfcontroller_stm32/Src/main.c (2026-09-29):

#include "main.h"


void RunTUDTask(void *param) {
	(void) param;

	while (1) {
		tud_task();
		vTaskDelay(pdMS_TO_TICKS(1));
	}
}


void ReadIncomingUSB(void *param) {
    (void) param;

    while (1) {
        if (ulTaskNotifyTake(pdTRUE, portMAX_DELAY)) {
        	while (tud_cdc_available() > 0) {
				uint8_t buff[512];
				uint32_t count = tud_cdc_read(buff, sizeof(buff));
				ParseUSBBytes(buff, count);
			}
        }
    }
}


void ReadIncomingLAMBDA80(void *param) {
	(void) param;

    while (1) {
        if (ulTaskNotifyTake(pdTRUE, portMAX_DELAY)) {
			if (xSemaphoreTake(SPIRfMutex, pdMS_TO_TICKS(50)) != pdTRUE) {
				printf("[ERROR] LAMBDA80 read timed out due to unreleased SPI mutex\n");
				return;
			}

			// Store interrupt status
			uint16_t irq = LAMBDA80_GetIRQStatus(&hspi3_rf, false);

			// Clear Rx interrupt
			LAMBDA80_ClearIRQ(&hspi3_rf, 0xFFFF, false);

			// Read the raw bytes from the radio buffer
			uint8_t len = 0;
			uint8_t start = 0;
			LAMBDA80_GetRxBufferStatus(&hspi3_rf, &len, &start, false);

			uint8_t buff[256];
			LAMBDA80_ReadBuffer(&hspi3_rf, buff, start, len, false);

			xSemaphoreGive(SPIRfMutex);

			// Decode raw bytes into a net packet
			NetPacket pkt;
			DecodeNetPacket(&pkt, buff, len);

			pkt.pktstatus = 1;   // Set 2.4GHz freq source bit
			pkt.pktstatus |= ((irq >> 5) & 2);   // Set CRC error bit

			// Place into the radio response queue
			if (xQueueSend(RadioResponseQueue, &pkt, pdMS_TO_TICKS(10)) != pdPASS) {
				printf("[ERROR] Radio response queue full\n");
			}
        }
    }
}


void ReadIncomingLAMBDA62(void *param) {
	(void) param;

    while (1) {
        if (ulTaskNotifyTake(pdTRUE, portMAX_DELAY)) {
        	if (xSemaphoreTake(SPIRfMutex, pdMS_TO_TICKS(50)) != pdTRUE) {
        		printf("[ERROR] LAMBDA62 read timed out due to unreleased SPI mutex\n");
        		return;
        	}

			// Store interrupt status
			uint16_t irq = LAMBDA62_GetIRQStatus(&hspi3_rf, false);

			// Clear Rx interrupt
			LAMBDA62_ClearIRQ(&hspi3_rf, 0xFFFF, false);

			// Read the raw bytes from the radio buffer
			uint8_t len = 0;
			uint8_t start = 0;
			LAMBDA62_GetRxBufferStatus(&hspi3_rf, &len, &start, false);

			uint8_t buff[256];
			LAMBDA62_ReadBuffer(&hspi3_rf, buff, start, len, false);

			xSemaphoreGive(SPIRfMutex);

			// Decode raw bytes into a net packet
			NetPacket pkt;
			DecodeNetPacket(&pkt, buff, len);

			pkt.pktstatus = 0;   // Set 868MHz freq source bit
			pkt.pktstatus |= ((irq >> 5) & 2);   // Set CRC error bit

			// Place into the radio response queue
			if (xQueueSend(RadioResponseQueue, &pkt, pdMS_TO_TICKS(10)) != pdPASS) {
				printf("[ERROR] Radio response queue full\n");
			}
        }
    }
}


void TransactionManagerTask(void *param) {
	(void) param;

	// State to function mapping table
	static const TMStateHandler TMStateTable[TM_NUM_STATES] = {
	    [TM_STATE_IDLE] = HandleStateIdle,
	    [TM_ECHO_CMD] = HandleStateEchoCmd,
		[TM_STATUS_CMD] = HandleStateStatusCmd,
		[TM_DISC_CMD] = HandleStateDiscoveryCmd,
		[TM_PKTTEST_CMD] = HandleStatePktTestCmd,
		[TM_DATA_DOWNLOAD_CMD] = HandleStateDataDownloadCmd,
		[TM_TELEMETRY] = HandleStateTelemetryCmd,
		[TM_SETHOME] = HandleStateSetHomeCmd
	};

    TMState currState = TM_STATE_IDLE;
    USBPacket currCmd;
    NetPacket currRadResp;

    // Continuously execute the function that maps to the current state and update the current state
    while (1) {
    	currState = TMStateTable[currState](&currCmd, &currRadResp);
    }
}


TMState HandleStateIdle(USBPacket* pkt, NetPacket* resp) {
	// Wait for a command to arrive over USB
	if (xQueueReceive(CommandQueue, pkt, pdMS_TO_TICKS(50)) == pdPASS) {
		if (pkt->type == USB_MTYPE_ECHO) { return TM_ECHO_CMD; }
		if (pkt->type == USB_MTYPE_STATUS) { return TM_STATUS_CMD; }
		if (pkt->type == USB_MTYPE_DISCOVERY) { return TM_DISC_CMD; }
		if (pkt->type == USB_MTYPE_PKTTEST) { return TM_PKTTEST_CMD; }
		if (pkt->type == USB_MTYPE_DATA_DOWNLOAD) { return TM_DATA_DOWNLOAD_CMD; }
		if (pkt->type == USB_MTYPE_TELEMETRY_START) { return TM_TELEMETRY; }
		if (pkt->type == USB_MTYPE_SETHOME) { return TM_SETHOME; }
	}
	return TM_STATE_IDLE;
}


TMState HandleStateEchoCmd(USBPacket* pkt, NetPacket* resp) {
//	printf("Executing ECHO command\n");

	SendPacketUSB(pkt);
	return TM_STATE_IDLE;
}


TMState HandleStateStatusCmd(USBPacket* pkt, NetPacket* resp) {
//	printf("Executing STATUS command\n");

	pkt->payloadlen = 2;
	pkt->payload[0] = 0xFA;
	pkt->payload[1] = 0xBB;

	SendPacketUSB(pkt);
	return TM_STATE_IDLE;
}


TMState HandleStateDiscoveryCmd(USBPacket* pkt, NetPacket* resp) {
	// Initialise radio, send the discovery packet, and start the 500ms timer on first pass
	if (xSemaphoreTake(SPIRfMutex, pdMS_TO_TICKS(50)) != pdTRUE) {
		printf("[ERROR] DISCOVERY timed out due to unreleased SPI mutex\n");
		return TM_STATE_IDLE;
	}
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

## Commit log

2026-01-26 Updated development log with all progress so far
    [RangeTest.kicad_sch, rangetest_RAW_1767278719.xlsx]
2026-01-28 Began making avionics development PCB. Started with the power circuitry which uses a TPS563201 buck converter to provide a stable 3.3V DC source.
    [avionics_dev_board.kicad_pcb, avionics_dev_board.kicad_sch]
2026-01-28 Fixed missing trace on avionics dev pcb
    [avionics_dev_board.kicad_pcb]
2026-02-01 Fixed packet sequence miscouting error and finalised avionics component selections
    [avionics_dev_board.kicad_sch]
2026-02-02 Started designing stm32g474ret6 section of the PCB schematic. Done power supply, external crystal oscillator, and BOOT0 and NRST pins so far
    [avionics_dev_board.kicad_sch]
2026-02-04 Updated PCB schematic with sensors and storage devices
    [avionics_dev_board.kicad_sch]
2026-02-07 Avionics dev board schematic done
    [avionics_dev_board.kicad_sch]
2026-02-08 Updated component selections and footprints assigned
    [avionics_dev_board.kicad_pcb, avionics_dev_board.kicad_sch]
2026-02-09 First revision of avionics dev board PCB - needs routing fixes
    [avionics_dev_board.kicad_pcb, avionics_dev_board.kicad_sch]
2026-02-10 Avionics dev PCB revision 2 - improved stackup and routing
    [avionics_dev_board.kicad_pcb, avionics_dev_board.kicad_sch]
2026-02-10 Cleanup and refinements to avionics dev board PCB
    [avionics_dev_board-B_Cu.gbr, avionics_dev_board-B_Mask.gbr, avionics_dev_board-B_Paste.gbr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]
2026-02-11 Improved shielding of GPS RF trace and added 0 ohm resistors to switch SWD RX and TX if necessary
    [avionics_dev_board-B_Cu.gbr, avionics_dev_board-B_Mask.gbr, avionics_dev_board-B_Paste.gbr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]
2026-02-12 Added pull up/down resistors to some pins according to datasheet recommendations
    [avionics_dev_board.kicad_pcb, avionics_dev_board.kicad_sch]
2026-02-28 Bare metal startup code for STM32G431KB
2026-03-10 Log file update
    [avionics_dev_board.kicad_pcb, avionics_dev_board.kicad_sch]
2026-03-15 Avionics dev board V2
    [avionics_dev_board.kicad_pcb, avionics_dev_board.kicad_sch]
2026-03-15 Added power isolation jumper to regulator output and improved fuse placement
    [avionics_dev_board.kicad_pcb, avionics_dev_board.kicad_sch]
2026-04-01 Devlog update
    [avionics_dev_board.kicad_pcb, avionics_dev_board.kicad_sch]
2026-04-09 Improved LSM6DSR FIFO reading and small calibration + integration test
2026-04-10 Implemented basic FIFO data retreival from ADXL375 accelerometer
2026-04-19 Initialisation code for W25Q flash. Updated project plan and devlog
    [link_budget.xlsx]
2026-04-22 Implemented metadata read/write and page programming functions to the W25Q driver
2026-04-24 Finished first pass of all functions in the W25Q driver
2026-04-24 B Finished first pass of all functions in the W25Q driver
    Fixes:
    - Updated all functions to use the 5 global metadata variables instead of passing around a long list of pointers
    - Fixed pointer math in data reading section of W25Q_ReadMetadata() to use the safe address getting function
    - Fixed potential issue in W25Q_ReadMetadata() where the data end address could be one less than the data start address if no data is present (essentially marking every part of memory as filled with data)
    - Fixed the starting search address to 0x0 in W25Q_GetSafeMetadataAddress()
    - Removed default argument from W25Q_WriteMetadata() - (this is a C++ feature, not C!)
    - Fixed a bunch of small syntax errors
    - Fixe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
    [w25q.c]
2026-04-24 Fixed a few minor syntax errors in W25Q driver
    [w25q.c]
2026-04-24 Lots of bugfixing and further progress on W25Q driver
    - Fixed potential buffer overflow in read volume functions due to read
    length not being taken into account when transferring data into the
    buffer
    - Fixed an infinite loop in W25Q_GetSafeContiguousReadAddressWithOffset
    caused by checking the Offset variable rather than OffsetLeft
    - Fixed an infinite loop in W25Q_GetSafeContiguousWriteAddress when the
    data section is currently empty
    - Fixed an oversight in W25Q_WriteAppendData which caused data to skip
    the first byte of the data section if the data section was empty at
    the time of the write
    - Added a check in W25Q_WriteVolume to prevent the end address being
    safed if it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
    [main.c, main.h, w25q.c]
2026-04-25 Added new testing functions for W25Q - Added Test_W25Q_Initialisation which tests initialisation and reading of existing data on the chip - Added Test_W25Q_Logging which tests erasure of previous fli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
    All of these tests pass perfectly. Test logs in docs/dev_board_planning.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
2026-04-28 Started making some basic functions for the LAMBDA62 driver
2026-04-29 LAMBDA62 driver update - Added read and write register functions - Added a workaround to the initialisation function from section 15.2 of the SX1262 datasheet to improve handling of antenna mismatches
    [lambda62.c]
2026-04-29 Finished basic LAMBDA62 driver. Started porting over everything to make LAMBDA80 driver
2026-05-01 Finished all main functions of the LAMBDA80 driver
2026-05-01 Expanded data logging functionality - Moved NMEA parsing functions to the m10s driver to clean up the main file - Added 'AppendLogPacket' functions to each sensor driver to cleanly generate byte arra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
2026-05-02 Testing serial communication between NUCLEO G431KB board and a host PC - Made a quick project using cubeMX to initialise a NUCLEO G431KB board and send a test string over USART2 to a host PC via a vi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
2026-05-03 Basic data download link finished - no error correction yet - Made a few small python scripts for receiving data from the avionics unit - Fixed invalid 0 value for preamble length exponent in SetPack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
    [HostSerialReceiver_Binary.py, Simple_LoRa_Reciever_G431KB.ioc, adxl375.c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]
2026-05-04 Data decoding tests - Wrote a python script to decode the raw binary packets received from the avionics unit into useable data - Added responsiveness checks to all sensor initialisation functions
    There is currently an issue where the LSM6DSR does not seem to be
    logging packets. Investigation is under way.
    [DecodeBinary.py, adxl375.c, lsm6dsr.c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]
2026-05-05 Data recording and transmission bugfixing - Fixed LAMBDA62 DIO1 initialisation masking LSM6DSR EXTI interrupt line - Fixed wrong type encoding for MAX-M10S data packets
    [DecodeBinary.py, bmp581.c, m10s.c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]
2026-05-06 - Added functions to each sensor driver to pause data acquisition when not needed - Added a function to automatically structure and send UBX messages to the MAX-M10S module
2026-05-12 Command link plan and start of RF controller board
    [avionics_dev_board.kicad_sch, rf_controller.kicad_pcb, rf_controller.kicad_sch]
2026-05-13 PCB layout for RF controller And additional updates to schematic: - Added ESD protection to USB data lines - Fixed wrong placement of capacitors around LDO voltage regulator - Added extra user LED an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
    [rf_controller.kicad_pcb, rf_controller.kicad_sch]
2026-05-15 Finalised RF controller PCB layout
    [rf_controller-B_Cu.gbr, rf_controller-B_Mask.gbr, rf_controller-B_Paste.gbr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]
2026-05-15 Added GFSK initialisation and packet configuration functions to LAMBDA62 driver
2026-06-07 Set up RF controller project with FreeRTOS and TinyUSB integrations
    [24clip.stl, 868clip.stl, Enclosure base.stl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]
2026-06-08 Added full initialisation code for RF controller and ported over LAMBDA drivers
2026-06-09 Attempting to fix USB descriptor bug
    [main.c, tusb_config.h]
2026-06-10 USB descriptor bug fixed
    [main.c, main.h, tusb_config.h]
2026-06-13 Implemented a robust and extensible USB command handling framework for the RF controller. Also updated the serial terminal to be able to send and receive data as hex instead of ascii
    [rangetest_RAW_1767278719.xlsx]
2026-06-15 Added a microsecond timer and started converting radio driver functions to RTOS friendly versions
2026-06-16 Started implementing FreeRTOS for the main avionics board
2026-06-18 Tying to fix radio communication bugs
    [lambda62.c, main.c]
2026-06-20 Added a basic packet testing command (only 868MHz currently)
2026-06-21 Improved the packet testing mode to switch continuously between 868MHz and 2.4GHz
2026-06-22 Attempting to fix intermittent radio module unresponsiveness
    [lambda62.c, main.c]
2026-06-23 Fixed LAMBDA80 module intermittent Tx timeout and lockup during test packet response
    [lambda62.c, lambda80.c, main.c]
2026-06-26 Some bugfixing and refactoring of the RF controller and avionics packet handling code
    [24clip.stl, 868clip.stl, Enclosure.stl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]

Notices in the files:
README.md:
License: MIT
